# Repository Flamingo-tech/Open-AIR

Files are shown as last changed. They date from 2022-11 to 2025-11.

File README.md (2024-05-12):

# Open AIR

Open AIR is an open-source solution for home ventilation and management through Home Assistant integration. The objective of this project is to develop a versatile ecosystem of Home Assistant-compatible devices that can be easily installed in a wide variety of off-the-shelf ventilation systems, allowing seamless integration into your smart home setup.

The OpenAIR ecosystem is designed to offer the following capabilities:

* Humidity measurement within air ducts
* CO2 level detection in air ducts
* Temperature monitoring inside air ducts
* Default Wi-Fi connectivity
* Full compatibility and control with Home Assistant out of the box
* Adherence to open-source principles

The long-term vision for this project is to create a fully open-source ventilation system that can be 3D printed, preferably using recycled plastics as the primary material.

#### Open AIR Mini:
<p align="center">
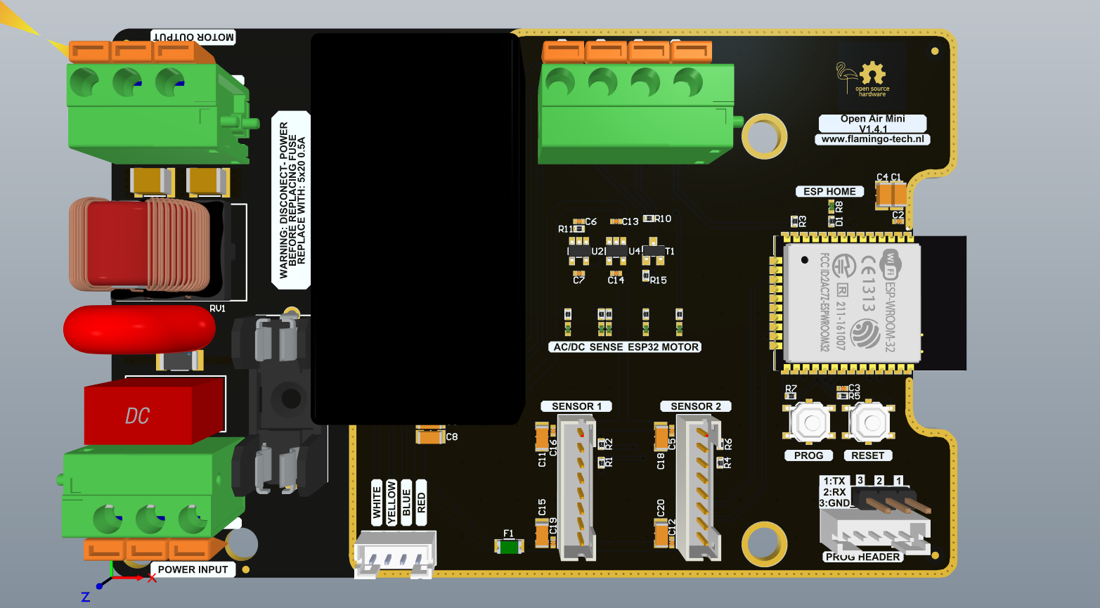
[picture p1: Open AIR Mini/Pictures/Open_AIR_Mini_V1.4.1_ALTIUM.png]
  
</p>

The OpenAIR Mini is a versatile, open-source ventilation controller designed to be compatible with a range of popular ventilation units, including but not limited to:

* DucoBox Silent Standard
* DucoBox Silent Perilex
* DucoBox Silent Connect
* DucoBox Focus (⚠ Note: Original Duco Valves are not supported! ⚠)
* Orcon MVS-15RH
    
Example intergration in HA:
<p align="center">
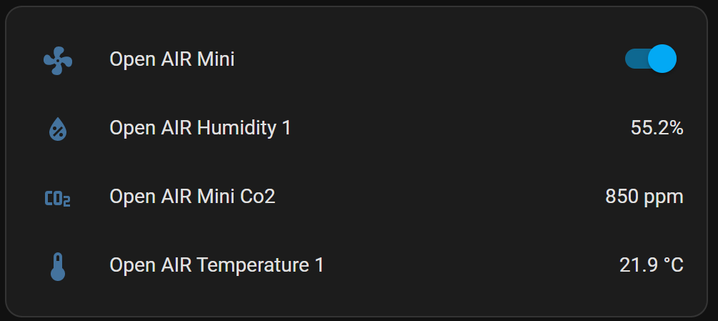
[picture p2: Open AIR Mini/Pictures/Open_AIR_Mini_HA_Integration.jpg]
  
</p>

For more information about the Open AIR Mini see: [Open AIR Mini](https://github.com/Flamingo-tech/Open-AIR/tree/main/Open%20Air%20Mini) 

#### Open AIR Valve:
<p align="center">
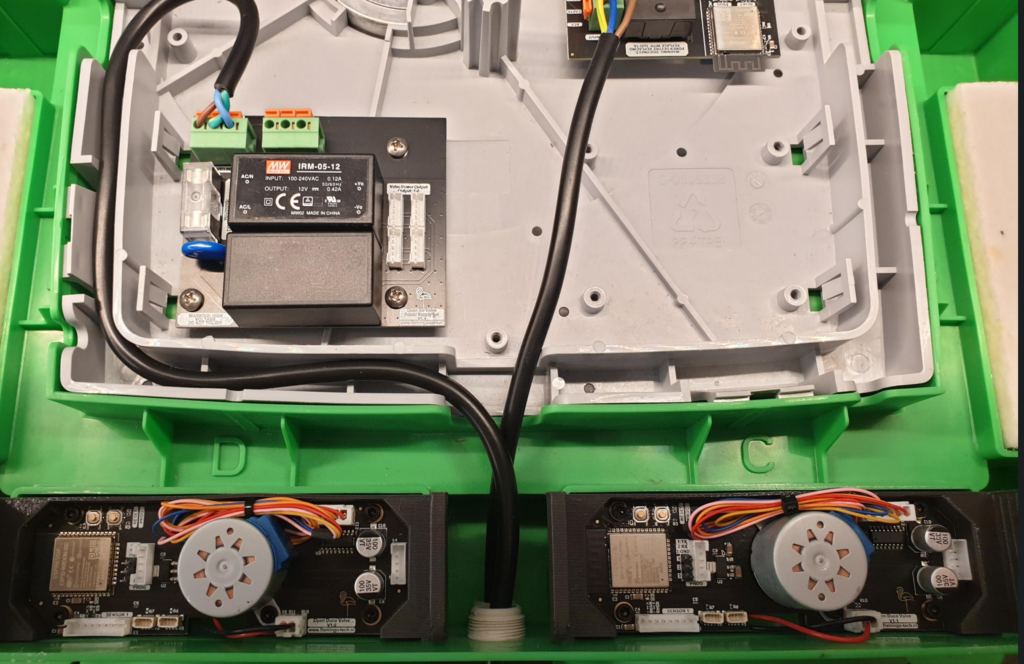
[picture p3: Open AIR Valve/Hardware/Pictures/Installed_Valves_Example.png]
  
</p>

The Open AIR Valve is an open-source valve designed to work with several Duco ventilation boxes, including the DucoBox Silent Standard, DucoBox Silent Perilex, DucoBox Silent Connect, and DucoBox Focus (Note: Original Duco Valves are not supported). It can be fully controlled from Home Assistant, allowing you to set any value between 0-100% open or closed. Additionally, the valve can be connected to one sensor. 

Example intergration in HA:
<p align="center">
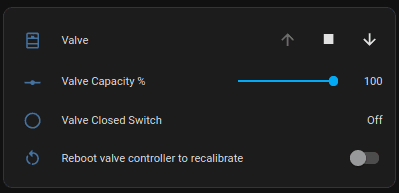
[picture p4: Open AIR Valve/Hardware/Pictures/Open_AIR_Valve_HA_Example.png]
  
</p>

In the future, an external enclosure will be developed for the OpenAIR Valves. This housing can be conveniently installed alongside any ventilation unit, positioned between the unit and the air duct for seamless integration.

For more information about the Open AIR Valve see: [Open AIR Valve](https://github.com/Flamingo-tech/Open-AIR/tree/main/Open%20AIR%20Valve) 

#### Open AIR Sensors
 TODO

# Progress:

| Part: |Done: |Version: |Duco Part Number:|Backwards compatible:|Active:|Store Link:|
|:---|:-----|:---|:---|:---|:---|:---|
|Open AIR Mini |✔️ |V1.3.0 | - |✔️ |✔️ |[Click](https://www.tindie.com/products/theflamingo/open-air-mini-v130/) 
|Open AIR Pro |❌ |- |- |- |❌ |
|Moisture Sensor |✔️ |V2.0.0 | 0000-4218 | ✔️ |✔️ |[Click](https://www.tindie.com/products/theflamingo/open-air-humidity-sensor/)
|CO2 Sensor |✔️ |V2.1.0 | 0000-4216 | ✔️ |❌ |
|Sense Board (RH,Co2,VOC, NOx)|✔️ |V1.0.0 | - | ❌ |✔️ |[Click](https://www.tindie.com/products/theflamingo/open-air-sense-board/)
|Programmer |✔️ |V1.1.0 | - | ✔️ |✔️ |
|Open AIR Valve |✔️ |V1.3.0 |- |❌ |✔️ |[Click](https://www.tindie.com/products/theflamingo/open-air-valve/)
|External Open AIR Valve |❌ |❌ |- |❌ |❌ | 

# Backwards Compatibility

If there is a checkmark in the 'Backwards Compatible' column of the table above, it indicates that you can use the specified device in conjunction with the original Duco Silent ventilation box. For example, you can replace the original Duco moisture/humidity sensor with one of our offerings.

# Special thanks:
[@thomasvnl](https://github.com/thomasvnl) For writing the Valve firmware and valuable feedback.\
[@Septillion](https://github.com/septillion-git) Thanks for providing valuable feedback.\
[@KristofRobberechts ](https://github.com/KristofRobberechts) For providing a beautiful valve design!\
[@slurpgeit](https://github.com/Slurpgeit) Helping write new firmware for the SHT-21 sensor + button software for the Open AIR Mini.

D.Smith For the first version of the installation manual

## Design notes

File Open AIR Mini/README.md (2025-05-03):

# Open AIR Mini

Open AIR Mini is an open-source project that aims to provide firmware and hardware for home ventilation boxes. The project has several goals, including open-source hardware and software, Wi-Fi connectivity, full controllability by Home Assistant, temperature-based ventilation, backward compatibility with Duco sensors, and support for different home ventilation boxes.

## The Hardware
<p align="center">
  
</p>
Open AIR mini installed on DucoBox system:
<p align="center">
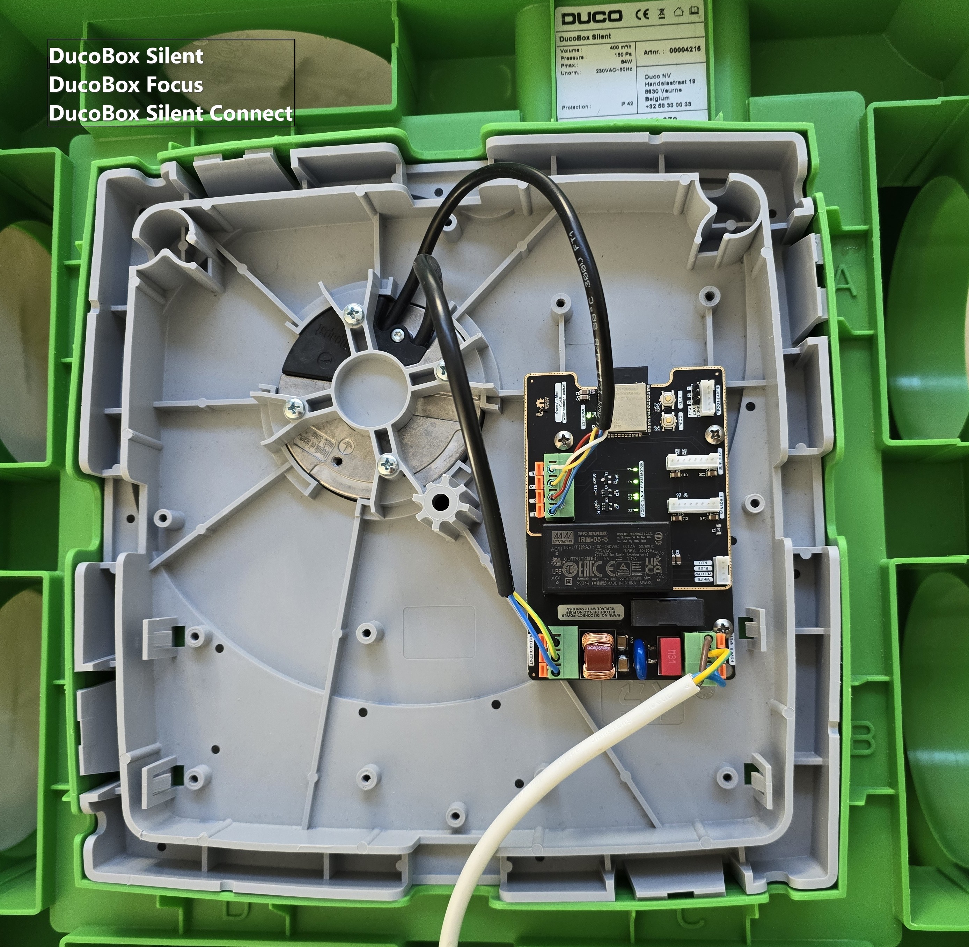
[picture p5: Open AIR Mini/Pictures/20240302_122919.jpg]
  
</p>
The Open AIR Mini hardware supports two sensors on the main board, Wi-Fi connectivity, Home Assistant integration via the ESPHome interface, OTA support, two sensor connectors, a robust power design, and status LEDs. The device is installed by connecting it to the ventilation box, and it can work with different home ventilation boxes. 

Open AIR mini installed on Orcon system:
<p align="center">
  
</p>
Since version V1.4.0 the Open AIR Mini can be directly installed in the ORCON MVS-15XX series of boxes. The original Orcon sensors and RF stuff is not supported! However we are working to make all the Open AIR Sensors compatible :)
On the Orcon systems only a single sensor is supported

### Status LEDS
<p align="center">
  
</p>

The Open AIR Mini from version V1.3.0 and above include five LEDs. The first LED (AC/DC) indicates the status of the Meanwell AC-> DC Converter, and if it is off, the device has no 230VAC power. The second and third LEDs (Sense LED and Sense LED 2) indicate the 5V and 3.3V sensor power, respectively. The fourth LED (ESP32 LED) indicates the 3.3V power supply for the ESP32, and the fifth LED (Motor) indicates the 10V output from the motor. All LEDs should be on in normal operation. 

The ESP32 has a status LED located under it, which displays three different statuses. It blinks slowly (about every second) when a warning is active, blinks quickly (multiple times per second) when an error is active, and stays off otherwise.

## Supported Ventilation Boxes
⚠No RF devices are supported⚠
The Open AIR Mini works with the following ventilation boxes:
 - DucoBox Silent Standard
 - DucoBox Silent Perilex
 - DucoBox Silent Connect
 - DucoBox Reno Non Perilex and Perilex
 - DucoBox Focus (Warning: Original Duco Valves are not supported!)
 - Orcon MVS-15xx
 - and more (see schematic below)
 
 If your home ventilation motor supports the following connections (See image below) Then you can use the Open Air Mini
  
 
The following pins need to be available:

230 Vac directly to the motor
 - 1 Protective earth
 - 2 Power Supply 230VAC 50-60Hz
 - 3 Neutral conductor
 
 Control cabling:
 - 4 GND (on ebmpapst motors BLUE)
 - 5 Tach output (on ebmpapst motors WHITE)
 - 6 10V Output (on ebmpapst motors RED)
 - 7 0-10V PWM Input (on ebmpapst motors YELLOW)

# ⚠ Important

Please note that this project is not supported by Duco and Orcon, and there is no affiliation or technical support from these companies. Modifying your ventilation box is done at your own risk.

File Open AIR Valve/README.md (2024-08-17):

# Open AIR Valve
The Open AIR Valve is an open-source valve designed to work with several Duco ventilation boxes, including the DucoBox Silent Standard, DucoBox Silent Perilex, DucoBox Silent Connect, and DucoBox Focus (Note: Original Duco Valves are not supported). It can be fully controlled from Home Assistant, allowing you to set any value between 0-100% open or closed. Additionally, the valve can be connected to one sensor. 

## The Hardware
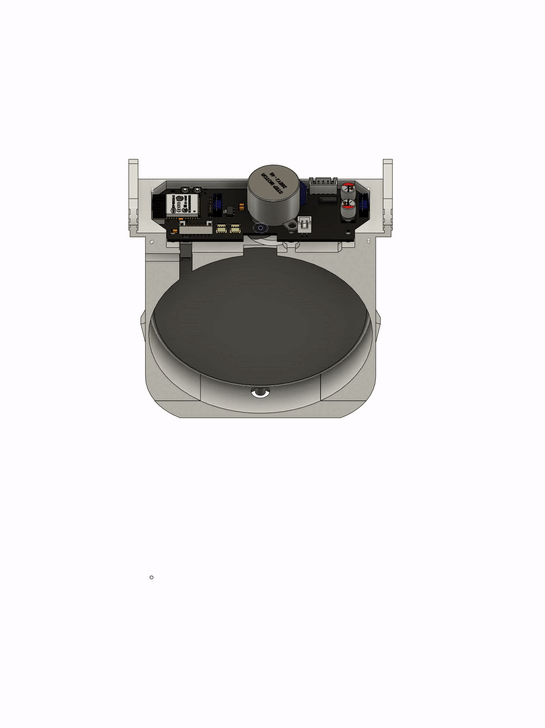
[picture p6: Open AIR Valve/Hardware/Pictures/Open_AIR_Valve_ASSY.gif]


Installed AIR Valve example:


### Status LEDs
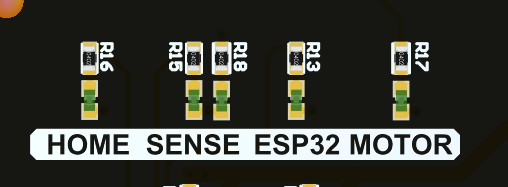
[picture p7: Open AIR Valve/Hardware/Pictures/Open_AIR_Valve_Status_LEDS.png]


The Open AIR Valve from version V1.3.0 and higher contains five LEDs. The first LED (HOME) indicates the status of the Home switch. When it is on, the valve is closed. The second and third LEDs (Sense LED and Sense LED 2) indicate the 5V and 3.3V sensor power, respectively. The fourth LED (ESP32 LED) indicates the 3.3V power supply for the ESP32, and the fifth LED (Motor) indicates the 12V power supply for the motor. All LEDs (except for the HOME LED, which depends on the position of the valve) should be on during normal operation.

# ⚠ Important

Please note that this project is not supported by Duco and Orcon, and there is no affiliation or technical support from these companies. Modifying your ventilation box is done at your own risk.

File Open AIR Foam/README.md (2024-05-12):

# AIR Foam
 Is a simple foam block that can be inserted into the following ducoboxes:
 - DucoBox Silent Standard
 - DucoBox Silent Perilex
 - DucoBox Silent Connect
 - DucoBox Focus
 
 This will silence your Ducobox a bit. I tested with a calibrated Mini DSP microphone and captured the before and after installation.
 
 This is at maximum speed (before foam):
 <p align="center">
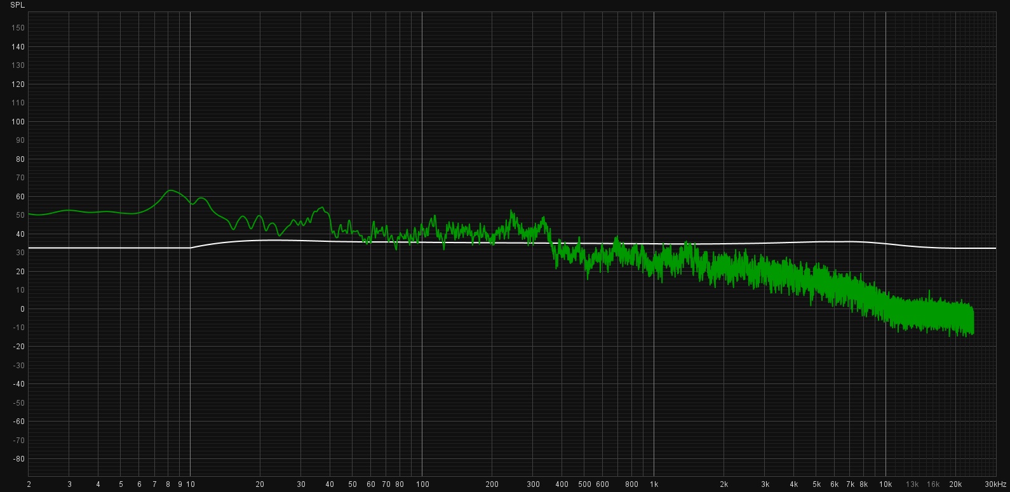
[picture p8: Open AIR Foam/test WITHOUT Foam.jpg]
  
</p>
 And then with foam installed:
 <p align="center">
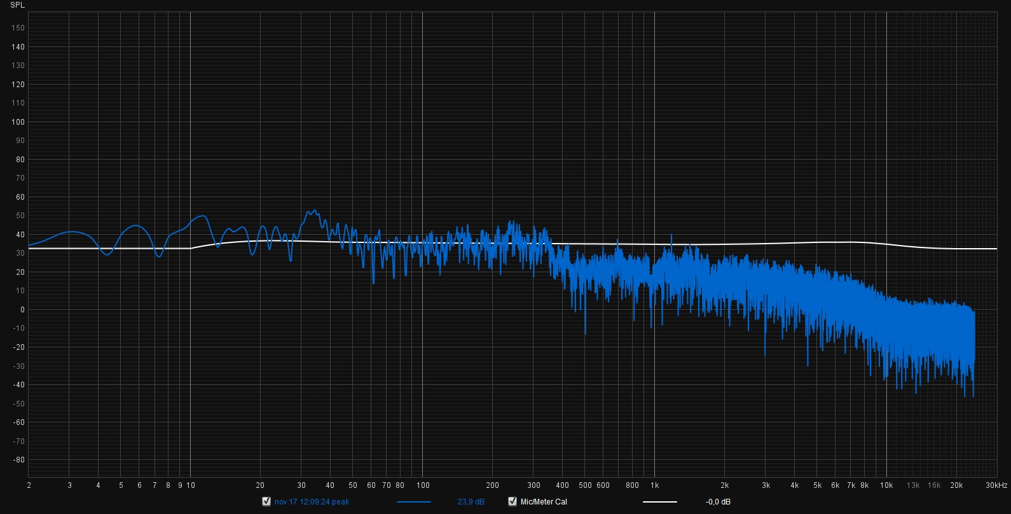
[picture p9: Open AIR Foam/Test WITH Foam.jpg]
  
</p>

 This foam has the following dimensions:
 
 Length: 15CM\
 Width: 12CM\
 Thickness: 4CM\
 Used foam: SG120
 
 You can buy it precut to the above size here : [Schuimwinkel](https://www.schuimwinkel.nl/polypress-sg-120-op-maat.html)

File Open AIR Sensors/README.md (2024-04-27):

PCB's and all files related to them are comming :)

Housing Step files can be found in the above folder! Happy printing!

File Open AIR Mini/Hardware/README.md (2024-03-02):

# Open AIR Mini Source Files
Welcome to the Open AIR Mini source files repository! This is where you can find all the necessary files for each release of Open AIR Mini.

Each release includes the following files:

**Assy Drawing:** text This file contains essential information about the PCBA layer stack, fabrication details, the size of the PCBA, component designators and their locations, as well as a 3D view of the part.

**Schematic Drawing:** This file provides the schematic of the PCBA, giving an overview of the circuit's connections.

**B.O.M File:** This file lists all the parts with their respective MPNs (manufacturer part numbers) and manufacturers, organized by designator.

**Gerber Files:** These files are used to order the bare PCBA's, allowing for accurate production of the circuit boards.

**Step File:** This file contains a 3D model of the PCBA, which can be used for visualization and design purposes.

We hope you find these files helpful in your project development process. Please feel free to contact us if you have any questions or feedback.

**Changelog:**
V1.3.X -> V1.4.0 & V1.4.1
Added support for Orcon MVS-15xx boxes. Now these boxes can be used without any modifications.

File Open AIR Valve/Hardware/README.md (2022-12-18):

# Open AIR Valve
Here you find the following:\
Open AIR Valve PCB Overview_A.pdf: An overview of all the connectors and pinouts used in the Open AIR Valve\
Open AIR Valve Assy B.O.M_A.pdf : An overview of all the different assembly parts needed to assemble a complete Open AIR Valve\
Open AIR Valve PCBA: Gerbers and Schematic op the Open AIR Valve\
Open AIR Valve 3D prints: The location for the 3D print files 

Happy making ^^

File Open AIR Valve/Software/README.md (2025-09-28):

# ESPHome Open Air Valve

Visit https://esphome.io/ for instructions on how to deploy this firmware.

More documentation might come available in future updates. Make sure to copy `example.secrets.yaml` to `secrets.yaml` and fill it with your own wifi credentials.

Change the "X" in `open-air-valve.yaml` with a number or a letter. This will help you identify the Open AIR Valves.

## Hall Sensor Homing

Since hardware version V1.4.0 of the Open AIR Valve , the Omron Switch is changed for a more reliable mechanism: A hall sensor.
The signal of the sensor is inverted! so a small change to your YAML file is needed if you upgrade.

```yaml
binary_sensor:
  - platform: gpio
    id: valve_homing_switch
    pin:
      number: GPIO35
      inverted: true #Change this to "false" if you hava a homing switch from pre V1.4.0 Open AIR Valve.
    name: "Valve Closed Switch"
```

## Sensors

The following sensors are supported right away, either via ESPHome or via a custom implementation.

### New Sensors:
All Valves are now shipped with these sensors:
1. [SHT-20](#sensor-support-SHT-20)
1. [SCD-40](#sensor-support-SCD-4X)
1. [SGP-41](#sensor-support-SGP-41)
1. [SCD-40 & SGP-41 Combination Sensor](#SCD-40-&-SGP-41-Combination-Sensor)

### Old Sensors:
1. [SHT-31](#sensor-support-sht-31)
1. [Senseair S8](#sensor-support-senseair-s8)
1. [SHT-31 & Senseair S8 Combination Sensor](#Using-the-Combination-Sensor-with-Senseair-S8-&-SHT-31-on-the-same-board)

## New:

### Sensor Support: SHT-20

If you have a SHT-20 Sensor add the following code at the bottom of `open-air-valve.yaml` 

```yaml
external_components:
  - source: github://dmaasland/esphome@sht2x
    components: [ sht2x ]
```

```yaml
  - platform: sht2x
    i2c_id: i2c_sensor_1
    temperature:
      name: "${upper_devicename} Temperature"
      id: air_temperature
      accuracy_decimals: 2
    humidity:
      name: "${upper_devicename} Humidity"
      id: air_humidity
      accuracy_decimals: 2
    update_interval: 30s
```
Thanks @dmaasland : https://github.com/dmaasland/esphome/tree/sht2x/esphome/components/sht2x

### Sensor Support: SCD-4X

More info about this sensor and ESPhome : https://esphome.io/components/sensor/scd4x.html

If you want to add a SCD-40 moisture & Temperature sensor & Co2 sensor to the Open AIR Mini, add the following code at the bottom of the `open-air-valve.yaml` file.

```yaml
sensor:
  - platform: scd4x
    i2c_id: i2c_sensor_1 
    co2:
      name: "${upper_devicename} CO2"
      id: air_Co2
      accuracy_decimals: 0
    temperature:
      name: " ${upper_devicename} Temperature"
      id: air_temperature
      accuracy_decimals: 2
    humidity:
      name: " ${upper_devicename} Humidity"
      id: air_humidity
      accuracy_decimals: 2
    update_interval: 30s
    measurement_mode: periodic
```

### Sensor Support: SGP-41

More info about this sensor and ESPhome : https://esphome.io/components/sensor/sgp4x.html & https://esphome.io/components/sensor/scd4x.html

If you want to add a combination sensor SCD-40 moisture & Temperature sensor & Co2 sensor & SGP-41 VOC & NOx to the Open AIR Mini, add the following code at the bottom of the `open-air-valve.yaml` file.

```yaml
sensor:
  - platform: sgp4x
    i2c_id: i2c_sensor_1 
    voc:
      name: "${upper_devicename} VOC Index"
      id: air_VOC
    nox:
      name: "${upper_devicename} NOx Index"
      id: air_NOx
    compensation:
      temperature_source: air_temperature #Make sure to match these if you change ID's.
      humidity_source: air_humidity       #Make sure to match these if you change ID's.
    update_interval: 30s
```

### Sensor Support: SCD-40 & SGP-41 Combination Sensor

More info about this sensor and ESPhome : https://esphome.io/components/sensor/sgp4x.html

If you want to add a SGP-41 VOC & NOx to the Open AIR Mini, add the following code at the bottom of the `open-air-valve.yaml` file.

```yaml
sensor:
  - platform: scd4x
    i2c_id: i2c_sensor_1 
    co2:
      name: "${upper_devicename} CO2"
      id: air_Co2
      accuracy_decimals: 0
    temperature:
      name: "${upper_devicename} Temperature"
      id: air_temperature
      accuracy_decimals: 2
    humidity:
      name: "${upper_devicename} Humidity"
      id: air_humidity
      accuracy_decimals: 2
    update_interval: 30s
    measurement_mode: periodic

  - platform: sgp4x
    i2c_id: i2c_sensor_1 
    voc:
      name: "${upper_devicename} VOC Index"
      id: air_VOC
    nox:
      name: "${upper_devicename} NOx Index"
      id: air_NOx
    compensation:
      temperature_source: air_temperature #Make sure to match these if you change ID's.
      humidity_source: air_humidity       #Make sure to match these if you change ID's.
    update_interval: 30s
```

## Old:

### Sensor Support: SHT-31

More info about this sensor and ESPhome : https://esphome.io/components/sensor/sht3xd.html

If you want to add a SHT-31 moisture & Temperature sensor to the Open AIR Mini, add the following code at the bottom of the `open-air-valve.yaml` file.

```yaml
sensor:
  - platform: sht3xd
    i2c_id: i2c_sensor_1
    temperature:
      name: "${upper_devicename} Temperature"
      id: air_temperature
    humidity:
      name: "${upper_devicename} Humidity"
      id: air_humdity
    address: 0x44
    update_interval: 60s
```

### Sensor Support: Senseair S8

More info about this sensor and ESPhome : https://esphome.io/components/sensor/senseair.html?highlight=co2+senseair

If you want to add a Senseair S8 Co2 sensor to the Open AIR Valve. Add the following code at the bottom of `open-air-valve.yaml` 

```yaml
sensor:
  - platform: senseair
    uart_id: uart_sensor_1
    co2:
      name: "${upper_devicename} CO2"
    update_interval: 60s
```

### Using the Combination Sensor with Senseair S8 & SHT-31 on the same board

If you want to use this specific combination sensor, add the following to the bottom of the `open-air-valve.yaml` file.

```yaml
sensor:
  - platform: sht3xd
    i2c_id: i2c_sensor_1
    temperature:
      name: "${upper_devicename} Temperature"
      id: air_temperature
    humidity:
      name: "${upper_devicename} Humidity"
      id: air_humidity
    address: 0x44
    update_interval: 60s
  - platform: senseair
    uart_id: uart_sensor_1
    co2:
      name: "${upper_devicename} CO2"
      id: air_co2
    update_interval: 60s
```

## Disconnected Mode

When Home Assistant cannot be reached, either because of a lack of WiFi connection or the Home Assistant server being unavailable, a `disconnected mode` has been added to provide basic functionality to the Open AIR Valve unit. This mode will allow the unit to continue standalone. When losing connection to Home Assistant or to your WI-FI network the valve will open automatically.

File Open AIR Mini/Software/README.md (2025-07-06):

# ESPHome Open AIR Mini

Visit https://esphome.io/ for instructions on how to deploy this firmware.

More documentation might come available in future updates. 

## Before you begin

Make sure to copy `example.secrets.yaml` to `secrets.yaml` and fill it with your own WiFi credentials.

## Different communication busses
Depending on what sensor is connected to what connector you need to declare the uart and/or I<sup>2</sup>C busses. If using one sensor, only one (uart/I<sup>2</sup>C) bus is required. In some cases, multiple busses are required for using multiple sensors with the same hardware id (for I<sup>2</sup>C) or if they do not support a hardware id (for uart).

For example, for uart:
```C++
#choose between:
uart_id: uart_sensor_1 // Only used for the Senseair S8 CO2 sensor (Original Duco Co2 Sensor)
uart_id: uart_sensor_2 // Only used for the Senseair S8 CO2 sensor (Original Duco Co2 Sensor)
```

For example, for I<sup>2</sup>C
```C++
i2c_id: i2c_sensor_1 // Used for RH , Co2 , Nox and VOc sensors
i2c_id: i2c_sensor_2 // Used for RH , Co2 , Nox and VOc sensors
```
Example:
```yaml
sensor:
  - platform: sht3xd
    i2c_id: i2c_sensor_1
    temperature:
      name: "Temperature Open AIR Mini x"
      id: air_temperature
    humidity:
      name: "Humidity Open AIR Mini x"
      id: air_humidity
    address: 0x44
    update_interval: 60s

#or
sensor:
  - platform: senseair
    uart_id: uart_sensor_1
    co2:
      name: "CO2 Open AIR Mini x"
    update_interval: 60s
```

## Sensors

The following sensors are supported right away, either via ESPHome or via a custom implementation.

### New Sensors:
All Open AIR Minis are now shipped with these sensors:
1. [SHT-4x](#sensor-support-SHT-4x)
1. [SCD-40](#sensor-support-SCD-4X)
1. [SGP-41](#sensor-support-SGP-41)
1. [SCD-40 & SGP-41 Combination Sensor](#SCD-40-&-SGP-41-Combination-Sensor)

### Old Sensors:
1. [SHT-31](#sensor-support-sht-31)
1. [Senseair S8](#sensor-support-senseair-s8)
1. [SHT-31 & Senseair S8 Combination Sensor](#Using-the-Combination-Sensor-with-Senseair-S8-&-SHT-31-on-the-same-board)
1. [SHT-20](#sensor-support-SHT-20)

## New:

### Sensor Support: SHT-4X

If you have a SHT-4X Sensor add the following code at the bottom of `open-air-mini.yaml` 

```yaml
sensor:
  - platform: sht4x
    i2c_id: i2c_sensor_1
    temperature:
      name: "Open AIR Mini x Temperature"
      id: air_temperature
      accuracy_decimals: 2
    humidity:
      name: "Open AIR Mini x Humidity"
      id: air_humidity
      accuracy_decimals: 2
    update_interval: 30s
```

### Sensor Support: SCD-4X

More info about this sensor and ESPhome : https://esphome.io/components/sensor/scd4x.html

If you want to add a SCD-40 moisture & Temperature sensor & Co2 sensor to the Open AIR Mini, add the following code at the bottom of the `open-air-mini.yaml` file.

```yaml
sensor:
  - platform: scd4x
    i2c_id: i2c_sensor_1 
    co2:
      name: "Open AIR Mini x CO2"
      id: air_Co2
      accuracy_decimals: 0
    temperature:
      name: " Open AIR Mini x Temperature"
      id: air_temperature
      accuracy_decimals: 2
    humidity:
      name: " Open AIR Mini x Humidity"
      id: air_humidity
      accuracy_decimals: 2
    update_interval: 30s
    measurement_mode: periodic
```

### Sensor Support: SGP-41

More info about this sensor and ESPhome : https://esphome.io/components/sensor/sgp4x.html & https://esphome.io/components/sensor/scd4x.html

If you want to add a combination sensor SCD-40 moisture & Temperature sensor & Co2 sensor & SGP-41 VOC & NOx to the Open AIR Mini, add the following code at the bottom of the `open-air-mini.yaml` file.

```yaml
sensor:
  - platform: sgp4x
    i2c_id: i2c_sensor_1 
    voc:
      name: "VOC Index Mini x"
      id: air_VOC
    nox:
      name: "NOx Index Mini x"
      id: air_NOx
    compensation:
      temperature_source: air_temperature #Make sure to match these if you change ID's.
      humidity_source: air_humidity       #Make sure to match these if you change ID's.
    update_interval: 30s
```

### Sensor Support: SCD-40 & SGP-41 Combination Sensor

More info about this sensor and ESPhome : https://esphome.io/components/sensor/sgp4x.html

If you want to add a SGP-41 VOC & NOx to the Open AIR Mini, add the following code at the bottom of the `open-air-mini.yaml` file.

```yaml
sensor:
  - platform: scd4x
    i2c_id: i2c_sensor_1
    co2:
      name: "Open AIR Mini Sensor Mini x CO2"
      id: air_Co2
      accuracy_decimals: 0
    temperature:
      name: "Open AIR Mini Sensor Mini x Temperature"
      id: air_temperature
      accuracy_decimals: 2
    humidity:
      name: "Open AIR Mini Sensor Mini x Humidity"
      id: air_humidity
      accuracy_decimals: 2
    update_interval: 30s
    measurement_mode: periodic

  - platform: sgp4x
    i2c_id: i2c_sensor_1 
    voc:
      name: "Open AIR Mini x VOC Index "
      id: air_VOC
    nox:
      name: "Open AIR Mini x NOx Index "
      id: air_NOx
    compensation:
      temperature_source: air_temperature #Make sure to match these if you change ID's.
      humidity_source: air_humidity       #Make sure to match these if you change ID's.
    update_interval: 30s
```

## Old:

### Sensor Support: SHT-31

More info about this sensor and ESPhome : https://esphome.io/components/sensor/sht3xd.html

If you want to add a SHT-31 moisture & Temperature sensor to the Open AIR Mini, add the following code at the bottom of the `open-air-mini.yaml` file.

```yaml
sensor:
  - platform: sht3xd
    i2c_id: i2c_sensor_1
    temperature:
      name: "Temperature Open AIR Mini x"
      id: air_temperature
    humidity:
      name: "Humidity Open AIR Mini x"
      id: air_humdity
    address: 0x44
    update_interval: 60s
```
### Sensor Support: SHT-20

If you have a SHT-20 Sensor add the following code at the bottom of `open-air-mini.yaml` 

```yaml
external_components:
  - source: github://dmaasland/esphome@sht2x
    components: [ sht2x ]
```

```yaml
  - platform: sht2x
    i2c_id: i2c_sensor_1
    temperature:
      name: "Open AIR Mini x Temperature"
      id: air_temperature
      accuracy_decimals: 2
    humidity:
      name: "Open AIR Mini x Humidity"
      id: air_humidity
      accuracy_decimals: 2
    update_interval: 30s
```
Thanks @dmaasland : https://github.com/dmaasland/esphome/tree/sht2x/esphome/components/sht2x

### Sensor Support: Senseair S8

More info about this sensor and ESPhome : https://esphome.io/components/sensor/senseair.html?highlight=co2+senseair

If you want to add a Senseair S8 Co2 sensor to the Open AIR Valve. Add the following code at the bottom of `open-air-valve.yaml` 

```yaml
sensor:
  - platform: senseair
    uart_id: uart_sensor_1
    co2:
      name: "CO2 Open AIR Mini x"
    update_interval: 60s
```

### Using the Combination Sensor with Senseair S8 & SHT-31 on the same board

If you want to use this specific combination sensor, add the following to the bottom of the `open-air-valve.yaml` file.

```yaml
sensor:
  - platform: sht3xd
    i2c_id: i2c_sensor_1
    temperature:
      name: "Temperature Open AIR Mini x"
      id: air_temperature
    humidity:
      name: "Humidity Open AIR Mini x"
      id: air_humidity
    address: 0x44
    update_interval: 60s
  - platform: senseair
    uart_id: uart_sensor_1
    co2:
      name: "CO2 Open AIR Mini x"
      id: air_co2
    update_interval: 60s
```

###  Notes on using multiple sensors

Change all the 'x' in the document to a number or a letter if you are using multiple sensors and want to be able to clearly identify which is which, and also to prevent conflicts in id namings. If sensors have identical names they wont show up in HA.

## Disconnected Mode

When Home Assistant cannot be reached, either because of a lack of WiFi connection or the Home Assistant server being unavailable, a `disconnected mode` has been added to provide basic functionality to the Open AIR Mini unit. This mode will allow the unit to continue standalone, which in combination with a humidity sensor even allows for different fan speeds activated by humidity levels.

### Disconnected Mode without Humidity Sensor

When the humidity sensor is not connected, the disconnected mode will only allow for the fan to run at a constant speed.

The fan speed can be set in the `open-air-mini.yaml` file by changing the global variable `disconnected_default_fan_speed` to a value between 0 and 100.

To use the Open AIR Mini in disconnected mode without a humidity sensor, in the `open-air-mini.yaml` file, make sure to use the `!include disconnected-mode-without-humidity-sensor.yaml` line in the `script` section. Make sure that the other include is commented out.

### Disconnected Mode With Humidity Sensor

When the humidity sensor is connected, the disconnected mode will allow for the fan to run at a variable speed based on the humidity level.

The different fan speeds and thresholds can be set in the `open-air-mini.yaml` file by changing the global variables that correspond to the different fan speeds and humidity thresholds (see inline comments).

To use the Open AIR Mini in disconnected mode with a humidity sensor, such a sensor has to be configured in the `open-air-mini.yaml`, and in the `script` section, make sure to use the `!include disconnected-mode-with-humidity-sensor.yaml` line. Make sure that the other include is commented out. The humidity sensor has to be connected to the Open AIR Mini, and the `id` of the humidity sensor has to be `air_humidity`.

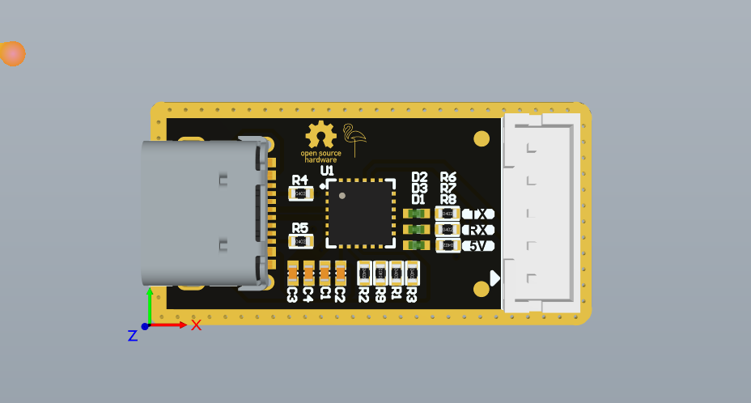
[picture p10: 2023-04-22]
Open AIR Programmer/Hardware/Pictures/Open_AIR_Programmer_V1.1.0.png

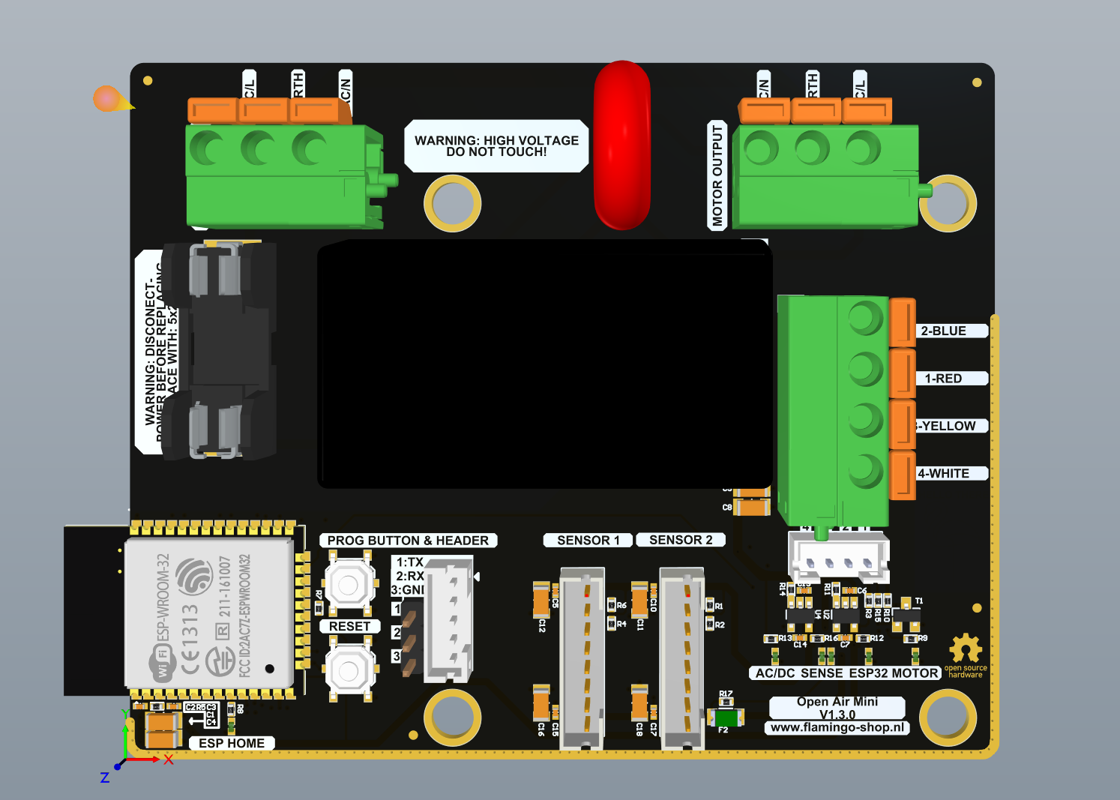
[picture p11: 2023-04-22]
Open Air Mini/Hardware/Pictures/Open_AIR_Mini_V1.3.0.jpg

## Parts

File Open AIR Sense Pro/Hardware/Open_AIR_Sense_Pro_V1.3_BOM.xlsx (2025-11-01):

Name | Description | Designator | Quantity
53261-0571 | Board Connector, 5 Contact(s), 1 Row(s), Male, Right Angle, 0.049 inch Pitch, Surface Mount Terminal, Locking, Natural Insulator, Receptacle | X7 | 1
B5B-ZR-SM4-TF | Header B5B-ZR-SM4-TF, 1.50mm, 5-contacts, top entry, SMT, /1000/reel | X6 | 1
HR911105A | 100mbit connector with integrated magnetics | X5 | 1
USB4105-GF-A-120 | USB Connector, 24 Contact(s), Female, Right Angle, Solder Terminal, Locking, Receptacle | X4 | 1
B8B-PH-SM4-TB(LF)(SN) | Connector Header, PH Series, 8 Position, 2.00mm, 100V, Surface Mount, Solder, Natural. | X3 | 1
687316124422 | FFC/FPC Connector, 16 Contact(s), 1 Row(s), Female, Straight, 0.02 inch Pitch, Surface Mount Terminal, Locking, Ivory Insulator | X2 | 1
SM04B-SRSS-TB(LF)(SN) | Connector Header, Side Entry, SR Series, 4 Position, 1.00mm, 50V, Surface Mount, Tin, Natural | X1 | 1
WS2812B-2020 | RGB Smart LED | U6, U7, U8, U9 | 4
LAN8720AI-CP-TR-ABC | Ethernet Transceiver | U5 | 1
AP2112K-3.3TRG1 | Fixed Positive LDO Regulator, 3.3V, 0.4V Dropout, CMOS, PDSO5 | U2, U3, U4 | 3
AP22653FDZ-7 | USB Load Switch | U1 | 1
PMZ550UNEYL | MOSFET N-Channel Enhancement SMD 30V 590mA 950mV 670mΩ DFN-1006-3 | T1 | 1
SMTSO20100CTJ | Steel Spacer, M2x10 | SP1, SP2 | 2
ERJ-2RKF1212X | RES ,SMT, 12.1kΩ, 1%, 100mW, 100ppm/°C 0402 | R19 | 1
ERJ-U020R00X | RES ,SMT, 0Ω, 1%, 100mW, 100ppm/°C 0402 | R18, R27 | 2
ERJ-2RKF49R9X | RES ,SMT, 49.9Ω, 1%, 100mW, 100ppm/°C 0402 | R14, R15, R16, R17 | 4
ERJ-2RKF1001X | RES ,SMT, 1kΩ, 1%, 100mW, 100ppm/°C 0402 | R5, R8, R20, R21 | 4
ERJ-2RKF1002X | RES ,SMT, 10kΩ, 1%, 100mW, 100ppm/°C 0402 | R3, R4, R6, R7, R11, R12, R13, R22, R23, R24, R25 | 11
ERJ-2RKF5101X | RES ,SMT, 5.1kΩ, 1%, 100mW, 100ppm/°C 0402 | R1, R2, R9, R10, R26, R28 | 6
ESP32-WROOM-32E | WiFi-Modul 802.11/BT 2, 4-2, 5GHz 150Mb/s | MD1 | 1
74279204 | Ferrite Bead, 1 Function(s), 0.5A, 2 Pin(s) | FB1 | 1
ESD9X5.0ST5G | Trans Voltage Suppressor Diode, 107W, 5V V(RWM), Unidirectional, 1 Element, Silicon | D3, D4, D5, D6 | 4
SMAJ5.0A-13-F | Trans Voltage Suppressor Diode, 400W, 5V V(RWM), Unidirectional, 1 Element, Silicon | D2 | 1
DT1240A-04LP-7 | Trans Voltage Suppressor Diode, 52W, 3.3V V(RWM), Unidirectional, 1 Element, Silicon | D1 | 1
CGA2B3X7R1H104K050BB | CAP MLCC 0402 100nF 10% 50V X7R 0402 | C25 | 1
GRM1555C1H9R0CA01D | CAP MLCC 0402 9pF 0.5% 50V C0G 0402 | C20, C21, C22, C23 | 4
CL05A106MQ5NUNC | CAP MLCC 0402 10uF 20% 6.3V X5R 0402 | C5, C6, C7, C8, C12, C13, C16, C17, C27, C28, C29, C30, C31, C32, C33 | 15
GRM155R61H105ME05D | CAP MLCC 0402 1uF 20% 25V X5R 0402 | C2, C9 | 2
CL05A475MP5NRNC | CAP MLCC 0402 4.7uF 20% 10vV X5R 0402 | C1, C3, C4, C10, C11, C14, C15, C18, C19, C24, C26 | 11

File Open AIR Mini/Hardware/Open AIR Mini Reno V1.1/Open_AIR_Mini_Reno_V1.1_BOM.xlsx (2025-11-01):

Name | Description | Designator | Quantity
CL05A106MQ5NUNC | CAP MLCC 0402 10uF 20% 6.3V X5R 0402 | C1, C2, C3, C9, C17, C18, C21, C22, C28, C29, C30, C31, C32, C33, C34, C36, C37 | 17
GRM155R61H105ME05D | CAP MLCC 0402 1uF 20% 25V X5R 0402 | C4 | 1
CL31A106KBHNNNE | CAP MLCC 1206 10uF 10% 50V X5R | C5, C7, C8 | 3
865230557006 | WCAP-AS5H Aluminum Electrolytic Capacitors | C6, C14 | 2
CGA2B3X7R1H104K050BB | CAP MLCC 0402 100nF 10% 50V X7R 0402 | C10 | 1
GRM1555C1H560JA01J | CAP MLCC 0402 56pF 5% 50V C0G 0402 | C11 | 1
GRM32EC81C476KE15K | CAP MLCC 1210 47uF 10% 16V X7R | C12, C13 | 2
CL05A475MP5NRNC | CAP MLCC 0402 4.7uF 20% 10vV X5R 0402 | C15, C16, C19, C20, C27, C35, C38 | 7
GRM1555C1H1R2BA01D | CAP MLCC 0402 1.2pF 0.1% 50V C0G 0402 | C23, C24, C25, C26 | 0
GRM155R71C103KA01D | CAP MLCC 0402 10nF 10% 16V X7R 0402 | C39, C40 | 2
150060WS75000 | SMD Mono-color Chip LEDs | D1, D4, D5, D8, D9, D11, D12 | 7
SMF24A | Trans Voltage Suppressor Diode, 200W, 24V V(RWM), Unidirectional, 1 Element, Silicon | D6 | 1
DT1240A-04LP-7 | Trans Voltage Suppressor Diode, 52W, 3.3V V(RWM), Unidirectional, 1 Element, Silicon | D7 | 1
BZT52C12-7-F | Zener Diode, 12V V(Z), 5.39%, 0.37W, Silicon, Unidirectional | D10 | 1
1206L050/24WR | PTC Resettable Fuse, Surface Mount | F1 | 1
74279204 | Ferrite Bead, 1 Function(s), 0.5A, 2 Pin(s) | FB1, FB2 | 2
74437336100 | General Purpose Inductor, 10uH, 20%, 1 Element, Powdered Iron-Core, SMD, 2220 | L1 | 1
ESP32-WROOM-32E | WiFi-Modul 802.11/BT 2, 4-2, 5GHz 150Mb/s | MD1 | 1
ERJ-2RKF1001X | RES ,SMT, 1kΩ, 1%, 100mW, 100ppm/°C 0402 | R1, R15, R16, R25, R30, R35, R37 | 7
ERJ-2RKF1801X | RES ,SMT, 1.8kΩ, 1%, 100mW, 100ppm/°C 0402 | R2, R3, R8, R9 | 4
ERJ-2RKF1002X | RES ,SMT, 10kΩ, 1%, 100mW, 100ppm/°C 0402 | R4, R5, R7, R10, R11, R17, R22, R23, R31, R32, R33, R34, R38, R40, R41 | 15
ERJ-2RKF3302X | RES ,SMT, 33kΩ, 1%, 100mW, 100ppm/°C 0402 | R6, R24 | 2
ERJ-2RKF1003X | RES ,SMT, 100kΩ, 1%, 100mW, 100ppm/°C 0402 | R12 | 1
ERJ-2RKF5101X | RES ,SMT, 5.1kΩ, 1%, 100mW, 100ppm/°C 0402 | R13 | 1
ERJ-2RKF1372X | RES ,SMT, 13.7kΩ, 1%, 100mW, 100ppm/°C 0402 | R14 | 1
ERJ-2RKF49R9X | RES ,SMT, 49.9Ω, 1%, 100mW, 100ppm/°C 0402 | R18, R19, R20, R21 | 4
ERJ-2RKF1212X | RES ,SMT, 12.1kΩ, 1%, 100mW, 100ppm/°C 0402 | R26 | 1
ERJ-U020R00X | RES ,SMT, 0Ω, 1%, 100mW, 100ppm/°C 0402 | R27, R28, R29, R36 | 4
0402WGF2200TCE | RES ,SMT, 220Ω, 1%, 63.5mW, 100ppm/°C 0402 | R39 | 1
PTS526SM15SMTR2LFS | Switch Tactile N.O. SPST Round Button Gull Wing 0.05A 12VDC 500000Cycles 1.57N SMD T/R | S1, S2 | 2
2N7002 | Small Signal Field-Effect Transistor, 0.115A I(D), 60V, 1-Element, N-Channel, Silicon, Metal-oxide Semiconductor FET | T1 | 1
SHT40-AD1B-R2 | Senserion Moisture and Temperature Sensor | U1 | 1
TPS54202DDCR | Switching Regulator, Current-mode, 2A, 500kHz Switching Freq-Max, PDSO6 | U2 | 1
AP2112K-3.3TRG1 | Fixed Positive LDO Regulator, 3.3V, 0.4V Dropout, CMOS, PDSO5 | U3, U4, U6 | 3
LAN8720AI-CP-TR-ABC | Ethernet Transceiver | U5 | 1
B5B-PH-SM4-TB(LF)(SN) | B5B-PH-SM4-TB(LF)(SN) | X1 | 1
M20-8770342 | Header SMT MALE 3 Pin 1 Row 2.54mm Pitch Vertical Gold Plated | X2 | 1
B8B-PH-SM4-TB(LF)(SN) | Connector Header, PH Series, 8 Position, 2.00mm, 100V, Surface Mount, Solder, Natural. | X3 | 1
B02P-NV(LF)(SN) | NV Series 2 Position 5 mm Pitch Through Hole Locking Header | X4 | 1
B4P-VH-B(LF)(SN) | Locking Header, Top Entry Type of PBT, 4 Circuit, 3.96mmPitch | X5 | 1
HR911105A | 100mbit connector with integrated magnetics | X6 | 1
B4B-PH-SM4-TB | 2.0mm pitch/Disconnectable Insulation displacement and Crimp style connectors | X7 | 1

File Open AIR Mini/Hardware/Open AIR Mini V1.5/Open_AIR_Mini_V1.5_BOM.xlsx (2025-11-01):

Name | Description | Designator | Quantity
CL31B226MPHNNNE | CAP CER SMT 22uF 20% 10V X7R 1206 | C1, C2, C5, C6, C7, C8 | 6
8853522130151 | Suppression Cap, 2200Pf, Class X1/Y2 | C3, C10 | 2
CL05A475MP5NRNC | CAP MLCC 0402 4.7uF 20% 10vV X5R 0402 | C4, C12, C13, C14, C15 | 5
890324023025CS | Film Capacitor | C9 | 1
150060WS75000 | SMD Mono-color Chip LEDs | D1, D2, D3, D4, D5, D6 | 6
1206L050/24WR | PTC Resettable Fuse, Surface Mount | F1 | 1
696103201002 | Fuses/Accessories | F2 | 1
744822110 | Data Line Filter, 2 Function(s), 250V, 1A, 4 Pin(s) | L1 | 1
BLM15HG102SN1D | Ferrite Chip, 1 Function(s), 0.25A, 2 Pin(s) | L2, L3, L4, L5, L6, L7, L8, L9 | 8
74279204 | Ferrite Bead, 1 Function(s), 0.5A, 2 Pin(s) | L10 | 1
PCB | PCB | PCB1 | 1
ERJ-2RKF1001X | RES ,SMT, 1kΩ, 1%, 100mW, 100ppm/°C 0402 | R1, R5, R20, R21 | 4
ERJ-2RKF1002X | RES ,SMT, 10kΩ, 1%, 100mW, 100ppm/°C 0402 | R2, R3, R4, R9, R10, R11, R17, R19 | 8
ERJ-U020R00X | RES ,SMT, 0Ω, 1%, 100mW, 100ppm/°C 0402 | R6, R7, R8 | 3
0402WGF2200TCE | RES ,SMT, 220Ω, 1%, 63.5mW, 100ppm/°C 0402 | R12 | 1
ERJ-2RKF2201X | RES ,SMT, 2.2kΩ, 1%, 100mW, 100ppm/°C 0402 | R13, R14, R15, R16, R22 | 5
CRCW20101M00FKEF | RES ,SMT, 1MΩ, 1%, 0.75W, 100ppm/°C 2010 | R18 | 1
B72214S301K101 | Varistor, Circuit Protection; 300Vrms; 775V; 4500A; Metal Oxide; 300pF; Wire; 0.6W; 25ns | RV1 | 1
PTS526SM15SMTR2LFS | Switch Tactile N.O. SPST Round Button Gull Wing 0.05A 12VDC 500000Cycles 1.57N SMD T/R | S1, S2 | 2
2N7002 | Small Signal Field-Effect Transistor, 0.115A I(D), 60V, 1-Element, N-Channel, Silicon, Metal-oxide Semiconductor FET | T1 | 1
IRM-05-5 | AC/DC 5W 5V Single Output Power Supply, Encapsulated Board Mount Module | U1 | 1
AP2112K-3.3TRG1 | Fixed Positive LDO Regulator, 3.3V, 0.4V Dropout, CMOS, PDSO5 | U2, U4 | 2
ESP32-WROOM-32E | WiFi-Modul 802.11/BT 2, 4-2, 5GHz 150Mb/s | U3 | 1
B5B-PH-SM4-TB(LF)(SN) | B5B-PH-SM4-TB(LF)(SN) | X1 | 1
M20-8770342 | Header SMT MALE 3 Pin 1 Row 2.54mm Pitch Vertical Gold Plated | X2 | 1
B4B-PH-SM4-TB | 2.0mm pitch/Disconnectable Insulation displacement and Crimp style connectors | X3 | 1
B8B-PH-SM4-TB(LF)(SN) | Connector Header, PH Series, 8 Position, 2.00mm, 100V, Surface Mount, Solder, Natural. | X4, X5 | 2
1790539 | Connector; PCB header; 15A; 320V; 4-position; FFKDSA/V1-5 08- 4 | X6 | 1
1790937 | Connector; PCB header; 15A; 320V; 3-position; FFKDSA/V1-5 08- 3 | X7, X8 | 2

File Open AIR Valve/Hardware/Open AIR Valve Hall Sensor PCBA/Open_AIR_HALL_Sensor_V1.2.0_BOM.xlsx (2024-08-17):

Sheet: Part List Report
 |  |  |  |  |  |  |  |  |  | V1.2.0
 | Bill of Material |  | Open AIR Valve Hall Sensor |  |  |  |  |  |  | <Parameter UpdateNumber not found>
 |  | Source Data From: | OPEN_AIR_VALVE_HALL_SENSOR.BomDoc
 |  | Project: | OPEN_AIR_VALVE_HALL_SENSOR.PrjPcb
 |  | Revision: | V1.2.0.<Parameter UpdateNumber not found>
 |  | Variant: | None
 | Report Date: |  | 17/08/2024 | 12:30
 | Print Date: |  | 2024-08-17 | 13:36:37
# | Print Date: | Quantity | Manufacturer | Manufacturer Part Number | Description | Value | Tolerance | #Column Name Error:' Fitted | Preferred Supplier
1 |  | 1 | Kemet | C0402C104K3RACTU | CAP MLCC 0402 100nF 10% 25V X7R 0402 | 100nF | 10%
2 |  | 1 | Murata | GCM155R71H104KE02J | CAP CER SMT 100nF 10% 50VDC X7R 0402 | 100nF | 10%
3 |  | 1 | Samsung | CL31B106KAHNFNE | CAP MLCC 1206 10uF 10uF 25V X7R 1206 | 10µF | 10%
4 |  | 2 | ONSemiconductor | ESD9X5.0ST5G | Trans Voltage Suppressor Diode, 107W, 5V V(RWM), Unidirectional, 1 Element, Silicon
5 |  | 2 | Panasonic | ERJ-S060R00V | RES ,SMT, 0Ω, 1%, 125mW, 100ppm/°C 0805 | 0 | 1%
6 |  | 1 | Texas Instruments | DRV5032FBDBZR | Hall Effect Sensor, 0.5mT Min, 4.8mT Max, -5.0-5.0mA, Plastic/epoxy, Rectangular, Surface Mount
7 |  | 1 | JST | B3B-XH-A(LF)(SN) | Connector Header, XH Series, 3 Position, 2.50mm, Through Hole, Press-Fit, Solder, Natural
Total: |  | 9 |  | Notes
 |  |  |  | <Parameter BOMNotes not found>

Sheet: Project Information
Project Full Path | C:\Users\Public\Documents\Altium\OPEN_AIR_VALVE_HALL_SENSOR\OPEN_AIR_VALVE_HALL_SENSOR.PrjPcb
Project Filename | OPEN_AIR_VALVE_HALL_SENSOR.PrjPcb
Variant Name | None
Data-Source Filename | OPEN_AIR_VALVE_HALL_SENSOR.BomDoc
Data-Source Full Path | OPEN_AIR_VALVE_HALL_SENSOR.BomDoc
Title | Bill of Materials for BOM Document [OPEN_AIR_VALVE_HALL_SENSOR.BomDoc]
Total Quantity | 9
Report Time | 12:30
Report Date | 17/08/2024
Report Date & Tine | 17/08/2024 12:30
Output Name | Bill of Materials
Output Type | BomReport
Output Generator Name | BOM
Output Generator Description | Bill of Materials

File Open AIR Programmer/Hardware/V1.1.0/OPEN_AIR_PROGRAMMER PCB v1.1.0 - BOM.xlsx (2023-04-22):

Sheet: Part List Report
 | Bill of material |  | Open AIR Programmer
 | Source Data From: |  | OPEN_AIR_PROGRAMMER PCB
 | Project: |  | OPEN_AIR_PROGRAMMER PCB
 | Revision: |  | 1.1.0
 | Variant: |  | None
 | Report Date: |  | 22-4-2023 | 15:31
 | Print Date: |  | 2023-04-22 | 15:35:12
# | Designator | Quantity | Manufacturer | Manufacturer Part Number | Description | Value | Tolerance | #Column Name Error:' Fitted | Preferred Supplier
1 | C1, C3 | 2 | KEMET | C0402C104K3RACTU | CAP CER SMT 100nF 10% 25V X7R 0402 | 100nF | 10%
2 | C2, C4 | 2 | Murata | GRM155R60J475ME47D | CAP CER SMT 4.7uF 20% 6.3V X5R 0402 | 4.7µF | 20%
3 | D1, D2, D3 | 3 | Wurth Electronics | 150040GS73240 | LED SMT Green Chip Waterclear 3.2V 20mA 0402
4 | J1 | 1 | GCT | USB4105-GF-A | USB 2.0 Type C Female Horizontal SMD, PD and USB2.0 only
5 | PCB1 | 1 | Open AIR Programmer | 1.1 | PCB
6 | R1, R2, R3, R8, R9 | 5 | Vishay | CRCW040210K0FKED | RES SMT 10kΩ 1% 62.5mW 100ppm/°C 0402 | 10kΩ | 1%
7 | R4, R5 | 2 | Bourns | CR0402-FX-5101GLF | RES SMT 5.1kΩ 1% 100mW 100ppm/°C 0402 | 5.1kΩ | 1%
8 | R6, R7 | 2 | Panasonic | ERJ-2RKF1001X | RES SMT 1kΩ 1% 100mW 100ppm/°C 0402 | 1kΩ | 1%
9 | U1 | 1 | Silicon Labs | CP2102N-A02-GQFN24 | USB2.0 to UART bridge SMT, 1 port, QFN-24
10 | X1 | 1 | JST | B5B-PH-K-S(LF)(SN) | JST (JAPAN SOLDERLESS TERMINALS) - B5B-PH-K-S(LF)(SN) - Pin Header, Wire-to-Board, 2 mm, 1 Rows, 5 Contacts, Through Hole, PH Series
Total: |  | 20 |  | Notes
 |  |  |  | No notes

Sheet: Project Information
Project Full Path | C:\Users\Public\Documents\Altium\Projects\Private_USB-UART\OPEN_AIR_USB-UART.PrjPcb
Project Filename | OPEN_AIR_USB-UART.PrjPcb
Variant Name | None
Data-Source Filename | OPEN_AIR_USB-UART.PrjPcb
Data-Source Full Path | C:\Users\Public\Documents\Altium\Projects\Private_USB-UART\OPEN_AIR_USB-UART.PrjPcb
Title | Bill of Materials for Project [OPEN_AIR_USB-UART.PrjPcb] (No PCB Document Selected)
Total Quantity | 20
Report Time | 15:31
Report Date | 22-4-2023
Report Date & Tine | 22-4-2023 15:31
Output Name | Bill of Materials
Output Type | BomReport
Output Generator Name | BOM
Output Generator Description | Bill of Materials

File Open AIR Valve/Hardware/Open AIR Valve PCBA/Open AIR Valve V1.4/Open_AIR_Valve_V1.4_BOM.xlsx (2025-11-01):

Name | Description | Designator | Quantity
CL31B226MPHNNNE | CAP CER 22uF 20% 10V X7R 1206 | C1, C5, C7, C10, C11, C13, C14, C15, C16, C17, C18 | 11
C0402C104K3RACTU | CAP CER 100nF 10% 25V X7R 0402 | C2, C4, C6, C12 | 4
GRM155C71A105KE11D | CAP CER 1uF 10% 10V X7S 0402 | C3, C8, C19 | 3
GRM155R60J475ME47D | CAP CER SMT 4.7uF 20% 6.3V X5R 0402 | C9, C20 | 2
150040GS73240 | LED SMT Green Chip Waterclear 3.2V 20mA 0402 | D1, D2, D3, D4, D5, D6 | 6
1206L050/24WR | Resettable fuse 0.5A/24V | F1 | 1
Fiducial |  | FID1, FID2, FID3, FID4 | 4
ERJ-2RKF1001X | RES SMT 1kΩ 1% 100mW 100ppm/°C 0402 | R1, R11, R13, R15 | 4
CRCW040210K0FKED | RES SMD 10kΩ 1% 62.5mW 100PPM 0402 | R2, R3, R10, R12, R14, R16, R17, R18 | 8
ERJ-2RKF2201X | RES SMD 2.2kΩ 1% 100mW 100PPM 0402 | R4, R5 | 2
CRCW04020000Z0EDC | RES SMD 0Ω 1% 62.5mW 100ppm/°C 0402 | R6, R7, R8, R9 | 4
PTS526 SMG15 SMTR2 LFS | Tactile Switch 50mA 12VDC, 5.2x5.2mm, 1.5mm H | S1, S2 | 2
ESP32-WROOM-32E | WiFi (802.11) & Bluetooth (v4.2) Module, SMD, 3.3V, Embedded Antenna | U1 | 1
AP2112K-3.3TRG1 | IC REG LDO 3.3V 0.6A SOT25 | U2, U4 | 2
ULQ2003D1013TR | Darlington Transistors Seven Darlington array | U3 | 1
B5B-PH-K-S(LF)(SN) | JST (JAPAN SOLDERLESS TERMINALS) - B5B-PH-K-S(LF)(SN) - Pin Header, Wire-to-Board, 2 mm, 1 Rows, 5 Contacts, Through Hole, PH Series | X1, X4 | 2
61300311121 | Board-To-Board Connector, Vertical, Wr-Phd Series, Through Hole, Header, 3, 2.54 mm | X2 | 1
B8B-PH-K-S(LF)(SN) | JST (JAPAN SOLDERLESS TERMINALS) - B8B-PH-K-S(LF)(SN) - Pin Header, Wire-to-Board, 2 mm, 1 Rows, 8 Contacts, Through Hole, PH Series | X3 | 1
B3B-XH-A(LF)(SN) | CONN HEADER VERT 3POS 2.5MM | X5 | 1
BM04B-SRSS-TB(LF)(SN) | Header SMT Male 4 Pin 1 Row 1.0mm Pitch Vertical Tin Plated | X6, X8 | 2
B5B-XH-AM(LF)(SN) | Header THT Male 5 Pin 1 Row 2.50mm Pitch Vertical tin Plated | X7 | 1

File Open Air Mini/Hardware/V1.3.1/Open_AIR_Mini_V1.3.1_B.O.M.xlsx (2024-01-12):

 |  |  |  |  |  |  |  |  |  | 1.3.1
 | Bill of material |  | Open AIR Mini |  |  |  |  |  |  | <Parameter UpdateNumber not found>
 | Source Data From: |  | Open_AIR_Mini_V1.3.1_PCB
 | Project: |  | Open_AIR_Mini_V1.3.1_PCB
 | Revision: |  | 1.3.1
 | Variant: |  | None
 | Report Date: |  | 10-4-2023 | 15:27
 | Print Date: |  | 2024-01-04 | 16:09:49
# | Designator | Quantity | Manufacturer | Manufacturer Part Number | Description | Value | Tolerance | #Column Name Error:' Fitted | Preferred Supplier
1 | C1, C4, C5, C8, C9, C11, C16, C18 | 8 | Samsung | CL31B226MPHNNNE | CAP CER 22uF 20% 10V X7R 1206 | 22uF | 20%
2 | C2, C10, C12, C15, C17 | 5 | KEMET | C0402C104K3RACTU | CAP CER 100nF 10% 25V X7R 0402 | 100nF | 10%
3 | C3, C6, C13 | 3 | Murata | GRM155C71A105KE11D | CAP CER 1uF 10% 10V X7S 0402 | 1uF | 10%
4 | C7, C14 | 2 | Murata | GRM155R60J475ME47D | CAP CER SMT 4.7uF 20% 6.3V X5R 0402 | 4.7µF | 20%
5 | D1, D2, D3, D4, D5, D6 | 6 | Wurth Electronics | 150040GS73240 | LED SMT Green Chip Waterclear 3.2V 20mA 0402
6 | F1 | 1 | Wurth Electronics | 696103101002 | FUSEHOLDER BLOCKS - PCB - CLIP C |  |  |  | Wurth Electronics
7 | F2 | 1 | Littelfuse | 1206L050/24WR | Resettable fuse 0.5A/24V
8 | PCB1 | 1 | Open AIR Mini | 1.3.1 | PCB
9 | R1, R2, R4, R6, R17 | 5 | Panasonic | ERJ-2RKF2201X | RES SMD 2.2kΩ 1% 100mW 100PPM 0402 | 2.2kΩ | 1%
10 | R3, R5, R7, R9, R10, R11, R13, R14, R15 | 9 | Vishay | CRCW040210K0FKED | RES SMD 10kΩ 1% 62.5mW 100PPM 0402 | 10kΩ | 1%
11 | R8, R12, R16 | 3 | Panasonic | ERJ-2RKF1001X | RES SMT 1kΩ 1% 100mW 100ppm/°C 0402 | 1kΩ | 1%
12 | RV1 | 1 |  |  | Varistor, Circuit Protection; 300Vrms; 775V; 4500A; Metal Oxide; 300pF; Wire; 0.6W; 25ns
13 | S1, S2 | 2 | C&K | PTS526 SMG15 SMTR2 LFS | Tactile Switch 50mA 12VDC, 5.2x5.2mm, 1.5mm H
14 | T1 | 1 | Nexperia | PMV16XNR | MOSFET, N-Channel, 6.8A, 20V, 16mΩ
15 | U1 | 1 | Espressif | ESP32-WROOM-32E (M113EH3200PS3Q0) | WiFi (802.11) & Bluetooth (v4.2) Module, SMD, 3.3V, Embedded Antenna
16 | U2, U4 | 2 | Diodes | AP2112K-3.3TRG1 | IC REG LDO 3.3V 0.6A SOT25
17 | U3 | 1 |  | IRM-05-5 | AC/DC 5W 5V Single Output Power Supply, Encapsulated Board Mount Module
18 | X1, X5 | 2 | Phoenix Contact | 1790937 | Connector; PCB header; 15A; 320V; 3-position; FFKDSA/V1-5 08- 3
19 | X2 | 1 | Phoenix Contact | 1790539 | Connector; PCB header; 15A; 320V; 4-position; FFKDSA/V1-5 08- 4
20 | X3 | 1 | JST | B5B-PH-K-S(LF)(SN) | JST (JAPAN SOLDERLESS TERMINALS) - B5B-PH-K-S(LF)(SN) - Pin Header, Wire-to-Board, 2 mm, 1 Rows, 5 Contacts, Through Hole, PH Series
21 | X4, X6 | 2 | JST | B8B-PH-K-S(LF)(SN) | JST (JAPAN SOLDERLESS TERMINALS) - B8B-PH-K-S(LF)(SN) - Pin Header, Wire-to-Board, 2 mm, 1 Rows, 8 Contacts, Through Hole, PH Series
22 | X7 | 1 | Wurth Elektronik | 61300311121 | Board-To-Board Connector, Vertical, Wr-Phd Series, Through Hole, Header, 3, 2.54 mm
23 | X8 | 1 | JST | B4B-PH-K-S(LF)(SN) | Header THT Male 4 Pin 1 Row 2mm Pitch Vertical Tin Plated
Total: |  | 60 |  | Notes
 |  |  |  | <Parameter BOMNotes not found>

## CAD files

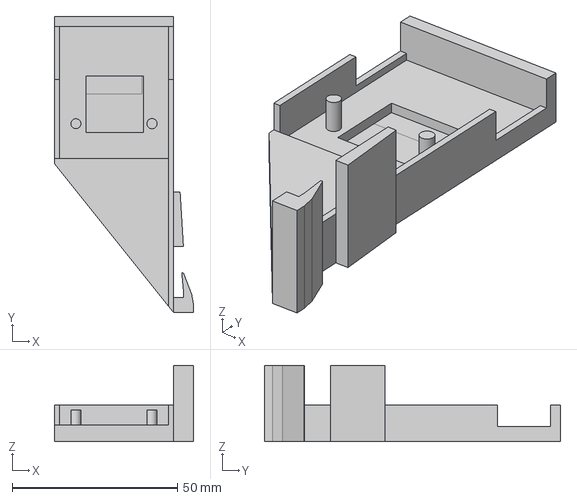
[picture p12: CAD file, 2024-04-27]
Open AIR Sensors/Open AIR Sensor Housing/Duco Sensor Housing/Open_AIR_Sensor_Housing_Duco_Bottom_B.step
42.1 x 89.5 x 23.0 mm

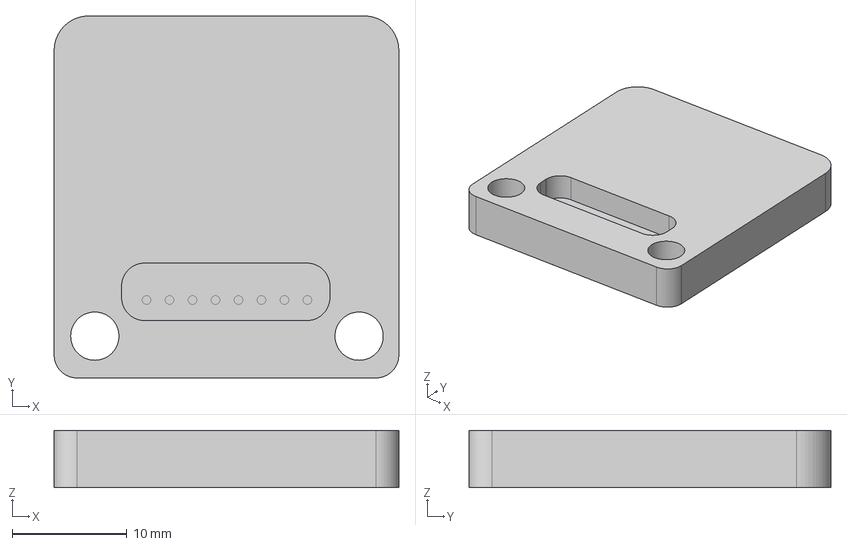
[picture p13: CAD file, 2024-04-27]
Open AIR Sensors/Open AIR Sensor Housing/Orcon Sensor Housing/Open_AIR_Sensor_Housing_Orcon_B.step
30.0 x 31.5 x 5.00 mm

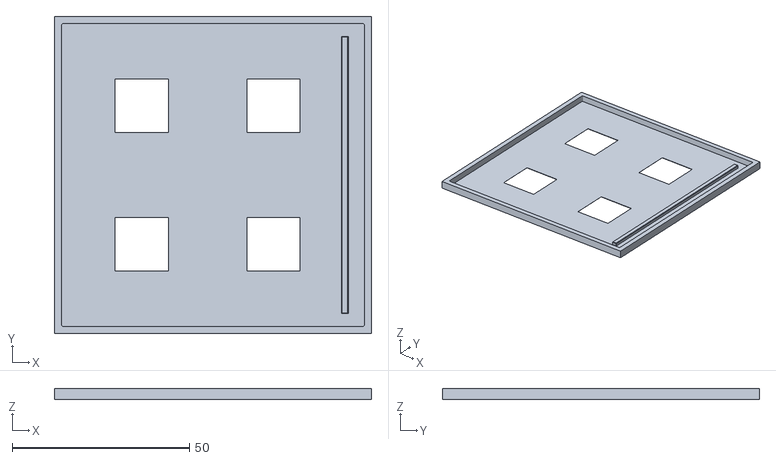
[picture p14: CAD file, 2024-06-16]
Open AIR Stickers/Sticker Align Jig/ESW-0ZAA-EU-Sticker Align Jig.obj
89.4 x 89.4 x 3.00

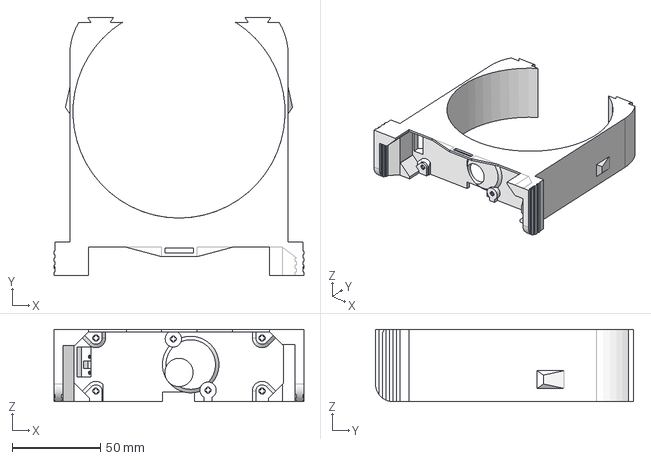
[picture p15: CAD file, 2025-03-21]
Open AIR Valve/Hardware/Open AIR Valve 3D prints/NEW (Hall Sensor)/Open_AIR_Valve_Top_C.step
141.4 x 146.0 x 40.9 mm

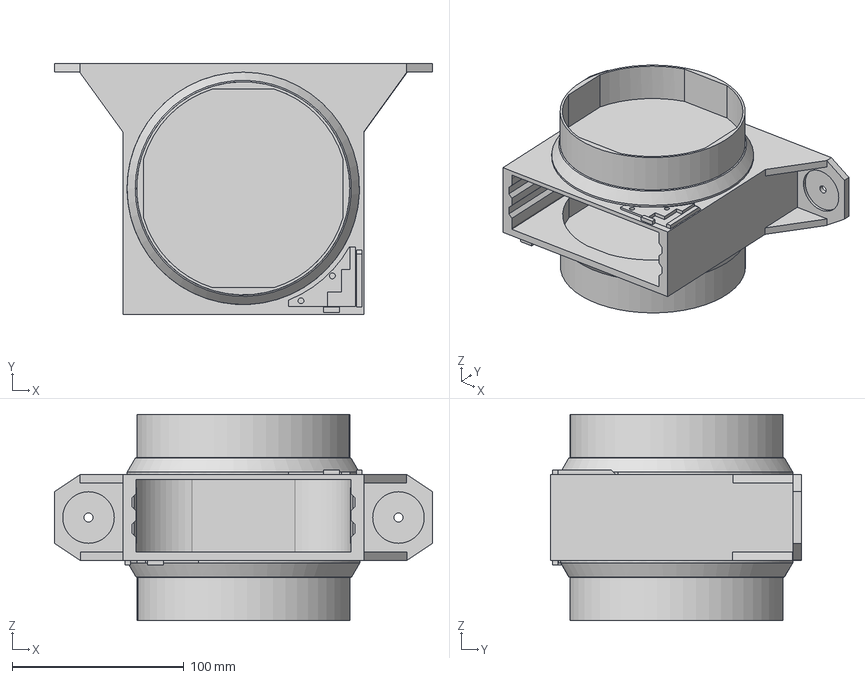
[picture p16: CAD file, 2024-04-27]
Open AIR Valve_External/Hardware/Open AIR Valve 3D prints/Open_AIR_Valve_External_Housing_A.step
220.0 x 146.0 x 120.0 mm

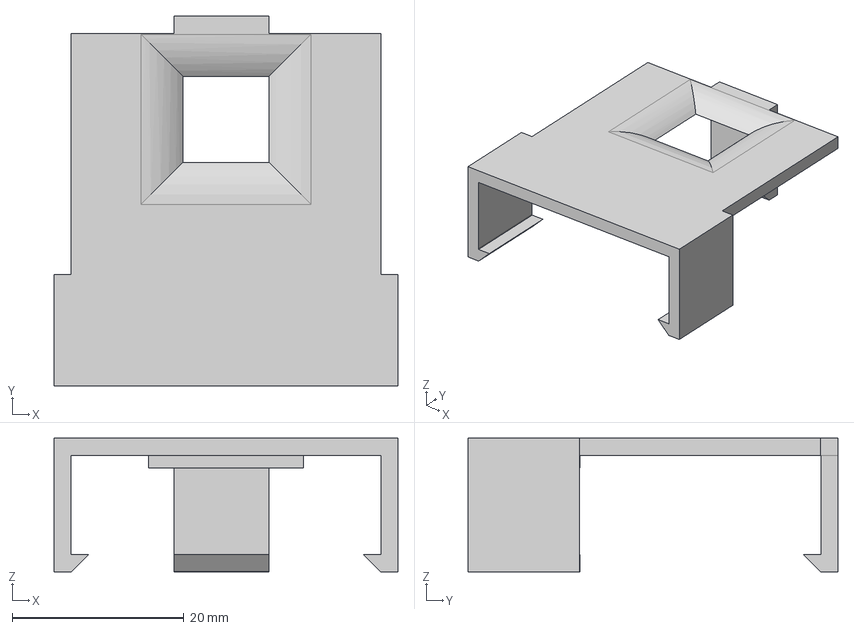
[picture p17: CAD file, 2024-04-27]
Open AIR Sensors/Open AIR Sensor Housing/Duco Sensor Housing/Open_AIR_Sensor_Housing_Duco_Top_B.step
40.0 x 43.0 x 15.6 mm

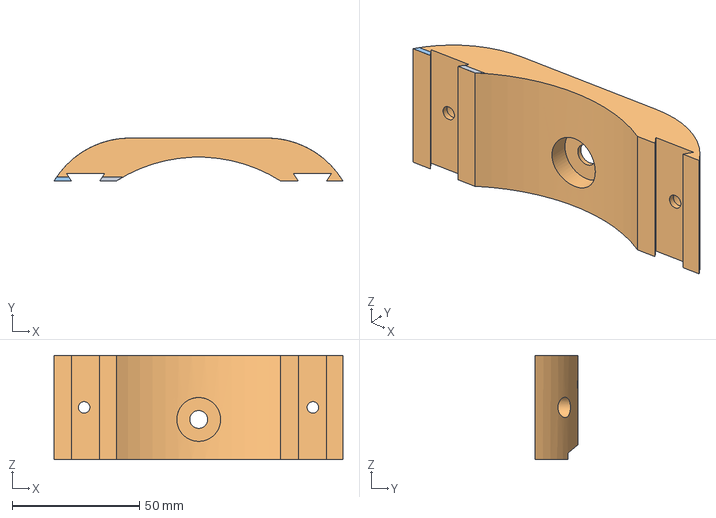
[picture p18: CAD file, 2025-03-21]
Open AIR Valve/Hardware/Open AIR Valve 3D prints/NEW (Hall Sensor)/Open_AIR_Valve_Bottom_C.step
113.4 x 16.9 x 40.9 mm

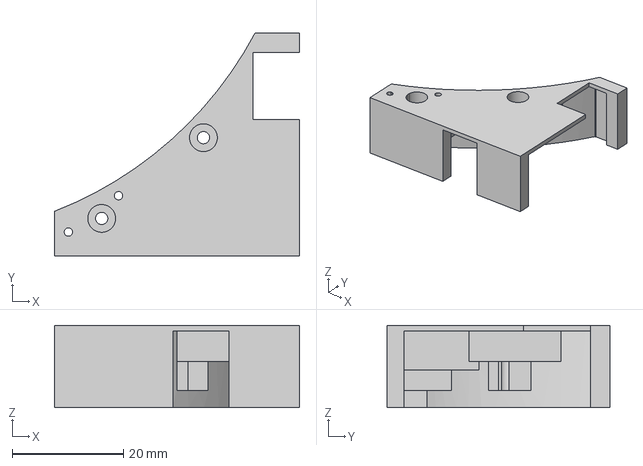
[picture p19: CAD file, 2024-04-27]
Open AIR Valve_External/Hardware/Open AIR Valve 3D prints/Open_AIR_Valve_External_PSU_Housing_A.step
44.0 x 40.0 x 14.8 mm

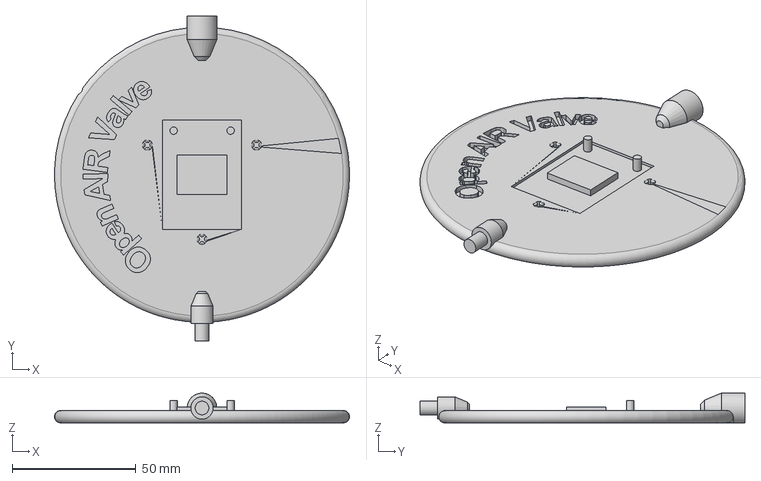
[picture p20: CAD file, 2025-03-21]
Open AIR Valve/Hardware/Open AIR Valve 3D prints/NEW (Hall Sensor)/Open_AIR_Valve_Disc_C.step
119.0 x 131.0 x 12.0 mm

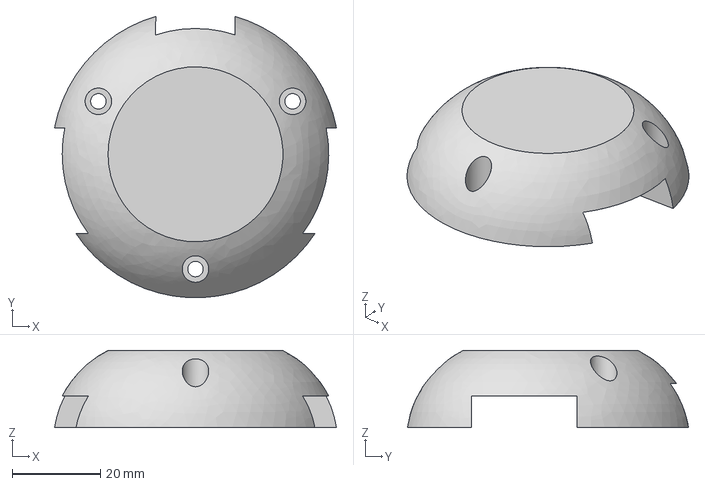
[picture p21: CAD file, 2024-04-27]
Open AIR Valve/Hardware/Open AIR Valve 3D prints/NEW (Hall Sensor)/Open_AIR_Valve_Sensor_Housing_A.step
63.9 x 63.7 x 17.5 mm

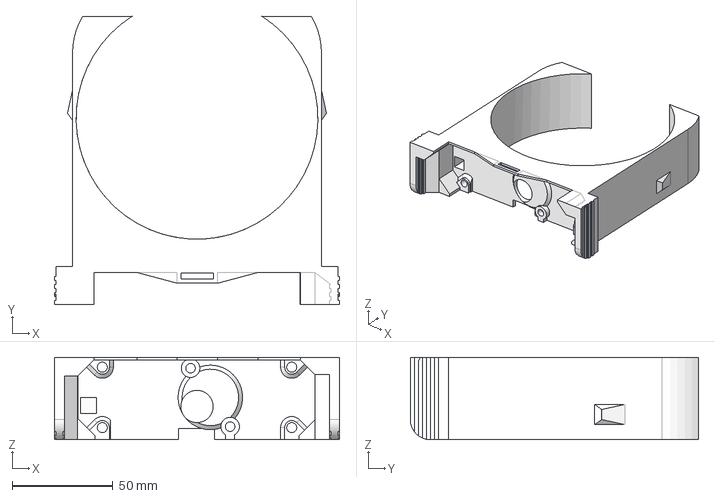
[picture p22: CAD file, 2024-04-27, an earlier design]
Open AIR Valve/Hardware/Open AIR Valve 3D prints/OLD (Omron Switch)/Open_AIR_Valve_Top_B.step
141.4 x 143.1 x 40.9 mm

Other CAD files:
Open AIR Valve/Hardware/Open AIR Valve 3D prints/OLD (Omron Switch)/Open_AIR_Valve_Bottom_A.step
Open AIR Valve/Hardware/Open AIR Valve 3D prints/OLD (Omron Switch)/Open_AIR_Valve_Disc_A.step

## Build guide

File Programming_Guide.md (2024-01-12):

# Programming Guide for Open AIR Devices

This guide provides detailed instructions for programming Open AIR Devices. There are three primary methods:

1. UART Programming.
2. OTA (Over-The-Air) from ESPHome.
3. OTA from a Web Browser.

**Warning**: Incorrect configurations can disable options 2 and 3. Exercise caution when applying custom YAML configurations.

## Option 1: UART Programming
To begin programming with UART, ESPHome needs to be installed on your computer or within Home Assistant (HA).

### Step 1: Install Python
- **Download Python for Windows**: Visit the [Windows Python Download Page](https://www.python.org/downloads/windows).
- **Installation**: Choose the latest Windows installer version (e.g., 3.9.9 64-bit). Ensure to select 'Add Python to PATH' during installation for easier command execution.

  Python Installer

  After installation, you should see a screen confirming the successful installation.

  Installation Success

### Step 2: Install ESPHome
- **Open Command Prompt**: Search for 'CMD' in the start menu, then press Enter or click the Command Prompt app.
- **Install Command**: In the Command Prompt, type `pip3 install esphome` and press Enter. Wait for the installation process to complete.

  ESPhome Installation

### Step 3: Connect Your Open AIR Device 

To connect your Open AIR Device, you have two options:
- Use an Open AIR Programmer.
- Use a 3.3V compatible USB-UART bridge.

Refer to the pinout diagram here: [Pinout Diagram](https://github.com/Flamingo-tech/Open-AIR/blob/main/Open%20AIR%20Valve/Hardware/Open%20AIR%20Valve%20PCB%20Overview_A.pdf)

All Open AIR Devices use the same pinout on the UART Debug Port.

### Step 4: Upload 

1. **Uploading Firmware**: 
   - Open the Command Prompt.
   - Type the command `esphome run YOURCONFIG.yaml` (replace `YOURCONFIG.yaml` with your configuration file name).
   - Press Enter to start the process. 

   Note: The compilation might take some time.

2. **Selecting Upload Option**: 
   - After compilation, choose the appropriate upload option as shown below:
     
     Upload Option

   - Press the number corresponding to the correct COM port option, followed by Enter.

3. **Important Steps During Upload**: 
   - When the message "connecting" appears, press the program button on the Open AIR Device.
   - While holding the program button, press the Reset button once.

   Following these steps will initiate the uploading process.

## Option 2: OTA (Over-The-Air) from ESPHome

Follow the Option 1 Esphome installation tutorial.

1. **Uploading Firmware**: 
   - Open the Command Prompt.
   - Type the command `esphome upload YOURCONFIG.yaml --device IP_OF_YOUR_DEVICE` 
     - Replace `YOURCONFIG.yaml` with your configuration file name.
     - Replace `IP_OF_YOUR_DEVICE` with your Open AIR device IP address.
     - Sometimes it will ask for an OTA password. By default, this is: `9f2ab9aa715f573e2476e75a5ec7f4e7`.      		
   - Press Enter to start the process. 

## Option 3: OTA (Over-The-Air) from the browser

Follow the Option 1 Esphome installation tutorial.

1. **Uploading Firmware**: 
   - Open your browser.
   - Navigate to the IP of your Open AIR Device, for example: `192.168.1.217`.
   - On the bottom of the page page is an OTA upload button. Press it.
   - You need to navigate to a binary generated by ESPHome. The easiest way to find it:
     - Open the Command Prompt.
     - Type the command `esphome run YOURCONFIG.yaml` (replace `YOURCONFIG.yaml` with your configuration file name).
     - Press Enter to start the process. 
     - When this process is finished, it will ask you how to upload the compiled binary. However, just above the successfully compiled program line is your BIN file location.
   - Go back to your browser and navigate to the file path given by ESPHome. Select the correct binary and press upload.

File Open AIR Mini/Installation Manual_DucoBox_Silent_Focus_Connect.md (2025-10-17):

 # Easy installation Manual For Open AIR Mini in Duco Systems

 **Special thanks to D.Smith for helping and inspiring me for writing this :)!**

 This guide assumes you've chosen the **pre-programmed** option when you've bought the Open AIR Mini. This guide will guide you trough the installation/Home Assistant proces.

 ## Introduction

The Open Air Mini is an innovative electronic circuit intended to replace the existing circuitry in your ventilation box. It is a product of an open-source endeavor aimed at giving you the power to control your preferred mechanical ventilation unit through your home automation system.

Typically, ventilation boxes, like those from DUCO or ORCON, can have their circuit boards upgraded with the Open Air Mini. This modification enables you to control your ventilation using a home automation system or even through a web browser.

The typical use case is to implement demand-driven ventilation. This system measures air quality factors such as CO2 and moisture. Based on these measurements, it adjusts the ventilation in your home. Consequently, it promotes energy efficiency by pausing the ventilation system's motor when not needed, and preventing the unnecessary expulsion of warm air from your home.

The Open Air Mini not only contributes to energy-saving but also provides freedom from vendor lock-in. It operates independently of cloud services and ensures your statistics remain private. It's a perfect blend of convenience, efficiency, and privacy.

**Important Notice**
Please be aware that this project operates independently and does not have support or affiliation with Duco, Orcon, or any other vendor. Moreover, there is no technical assistance available from these companies. If you choose to modify your ventilation box using the Open Air Mini, it is a decision made solely at your discretion and assumed risk. Remember, undertaking modifications implies accepting full responsibility for any potential consequences.

 ## Installation in a Ducobox Silent

 The installation proces is done in 7 easy steps!

 1. Locating Your Docubox Silent
 2. Remove Power
 3. Remove Original Hardware
 4. Insert Open AIR Mini
 5. Connect your Open AIR Mini
 6. Powering up Your Open AIR Mini
 7. Adding the Open AIR Mini to Home Assistant

# 1 Locating Your Docubox Silent

The location of your ventilation box can vary within your home. We encourage you to locate it. As a homeowner, this task should be straightforward and can be quite an enlightening step in familiarizing yourself further with your home's infrastructure. ;)
Please remove the white cover. You will be greated with:
<p align="center">
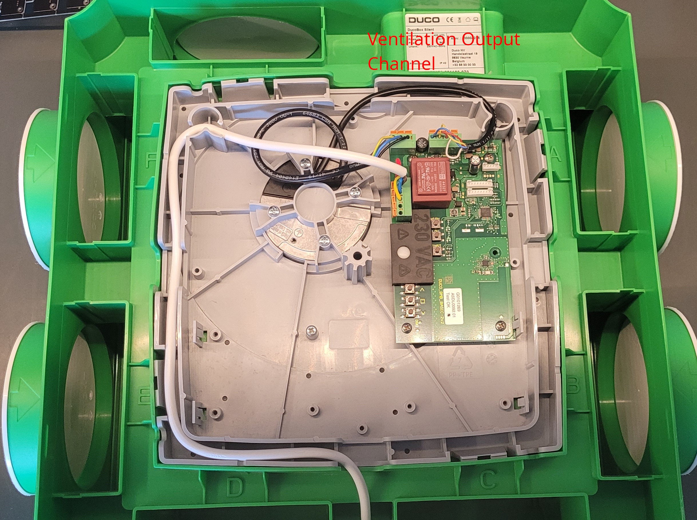
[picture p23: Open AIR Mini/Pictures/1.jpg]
  
</p>

# 2 Remove Power

It is critical to disconnect your Ducobox Silent before proceeding. This step is extremely important. **Neglecting to do so could result in severe injury or even death. Make sure to cut off all power supply.**

Ensure, then doubly ensure, that you've disconnected the correct plug. It's better to check multiple times than risk an accident.

If you're unsure about any aspect of these steps or find them confusing, don't hesitate to seek help. You might ask someone who's more familiar with the process, or consider hiring a professional. Safety should always be your top priority.
<p align="center">
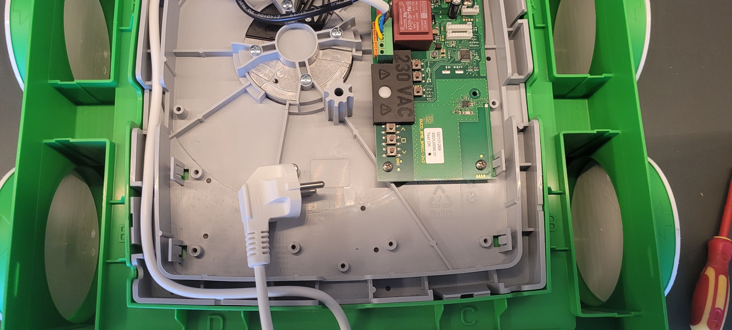
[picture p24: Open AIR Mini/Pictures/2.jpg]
  
</p>

Proceed to detach the cables from the original Ducobox hardware:
Press on the orange tabs (highlighted in red in the image provided) and gently pull the wires out from their respective connectors.
<p align="center">
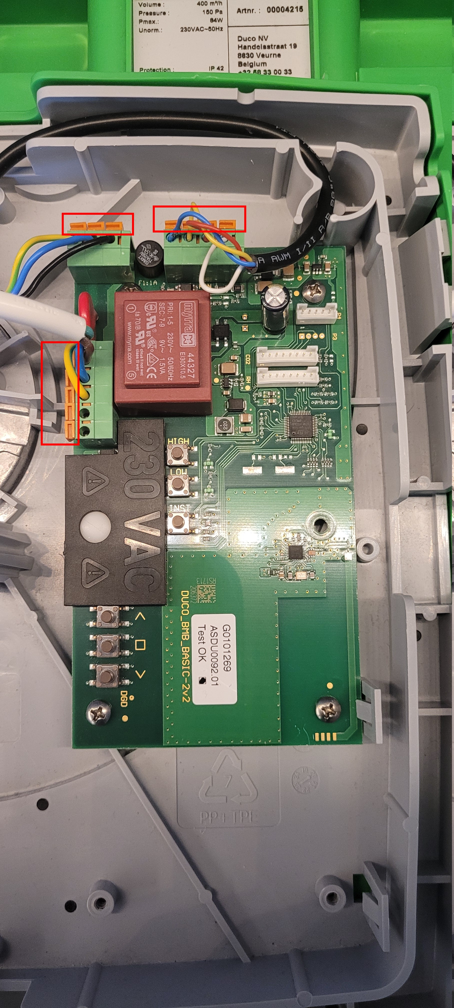
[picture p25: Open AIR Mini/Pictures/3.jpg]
  
</p>

When done it should look like this:
<p align="center">
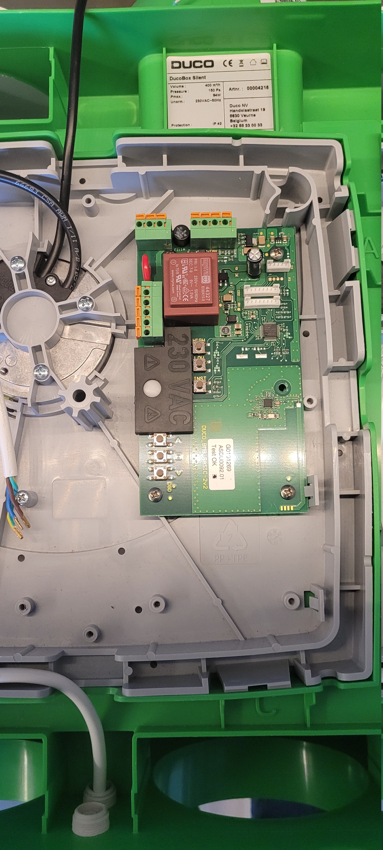
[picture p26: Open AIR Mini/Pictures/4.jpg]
  
</p>

# 3. Remove Original Hardware

Please use a screwdriver to carefully remove the four screws indicated in red in the image provided.
<p align="center">
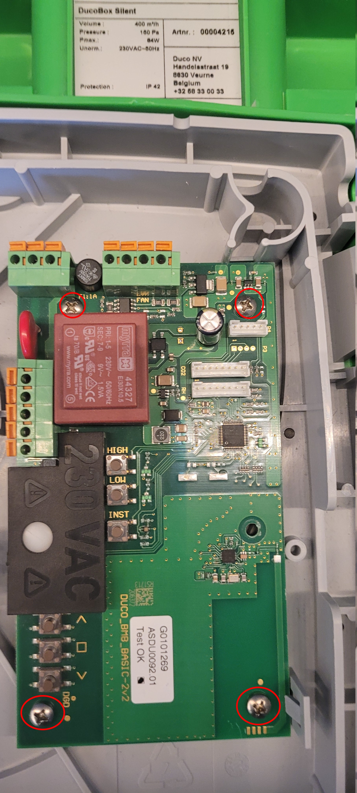
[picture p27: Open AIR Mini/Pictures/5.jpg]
  
</p>

Be sure to safely store the original circuit board after removal. If you ever decide to sell or rent your house in the future, you'll have the option to reinstall the original Duco hardware. Its availability will provide flexibility for future circumstances.

# 4. Insert Open AIR Mini

For the installation of the Open AIR Mini, position it as follows:
<p align="center">
  
</p>

Proceed to secure the Open AIR Mini by reinstalling the screws into the locations indicated in red:
<p align="center">
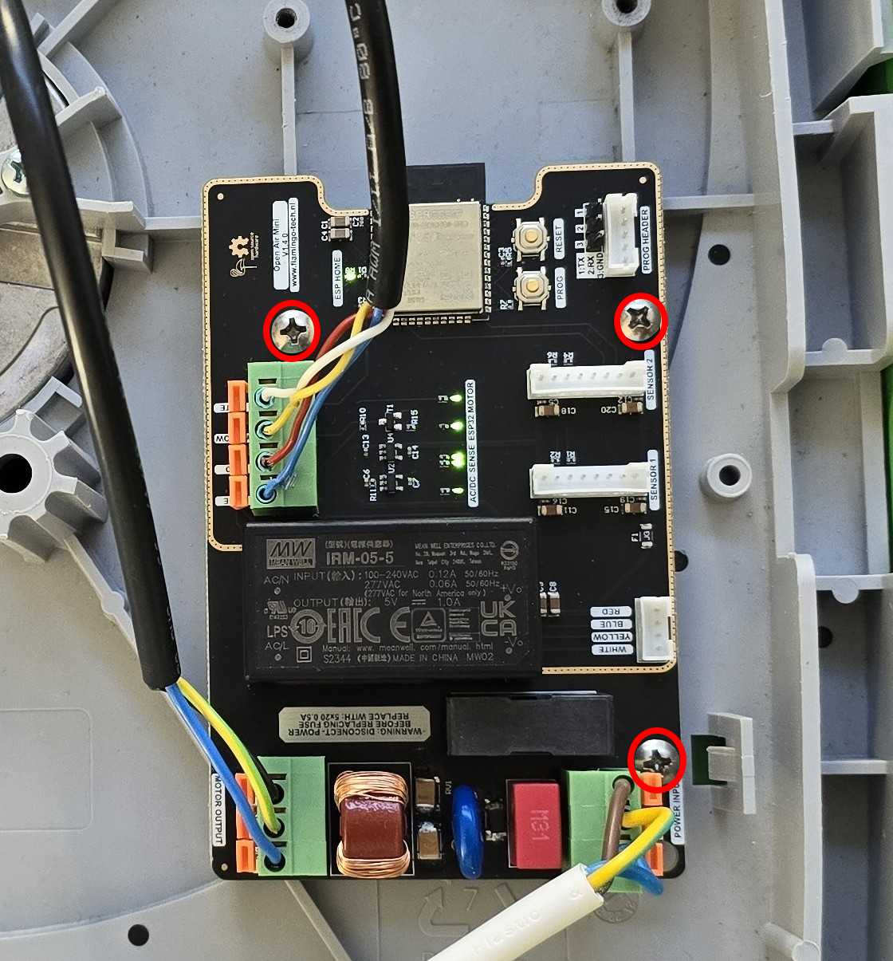
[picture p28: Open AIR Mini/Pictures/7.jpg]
  
</p>

# 5. Connect your Open AIR Mini

To provide power to your Open Air Mini, you'll need to connect the power cable to the bottom connector, which is colored green. **This is a crucial step: Press the orange tab and insert the cable simultaneously to ensure a solid connection.**

This process involves pushing the cable in as far as it will go. Once the cable is fully inserted, release the orange tab. Finally, give the cable a gentle pull to confirm it's securely connected. It's essential that the connection is firm to ensure proper operation.

<p align="center">
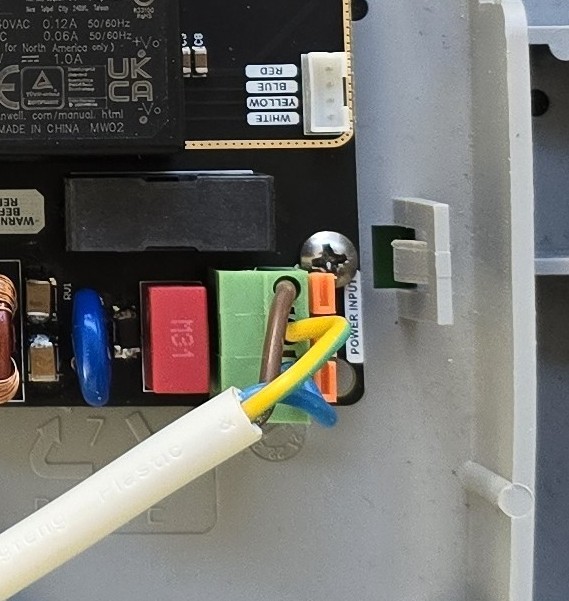
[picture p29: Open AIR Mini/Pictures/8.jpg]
  
</p>

Please pay close attention to the sequence in which the cables need to be connected!

After this connect the motor power:

<p align="center">
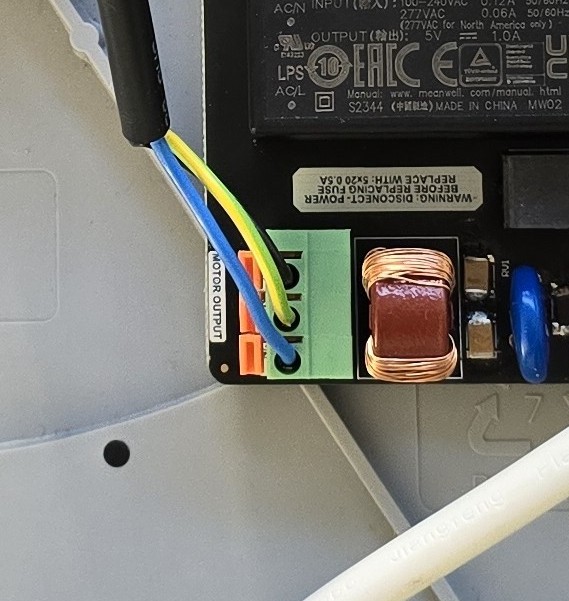
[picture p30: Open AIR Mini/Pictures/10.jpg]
  
</p>

Please pay close attention to the sequence in which the cables need to be connected!

Now connect the motor data cable:

<p align="center">
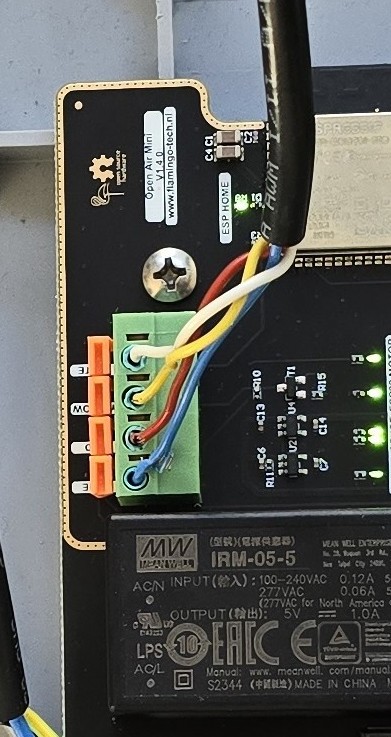
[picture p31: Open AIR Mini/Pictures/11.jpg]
  
</p>

Please pay close attention to the sequence in which the cables need to be connected!

Once all the cables are connected, make it a point to give each of them a gentle pull. This is to doubly ensure that they are firmly and correctly connected, providing a secure foundation for optimal operation.

# 6. Powering up Your Open AIR Mini

Reconnect the power plug to your Ducobox. You should now see a multitude of green LEDs light up.
Ensure that all five LEDs at the top of the circuit board are illuminated. If any of them are not on, please reach out to me at flamingo-tech@protonmail.com for assistance.
If you have the **pre-programmed option**, the ESPHome LED (marked by the lower green LED) should be blinking.
<p align="center">
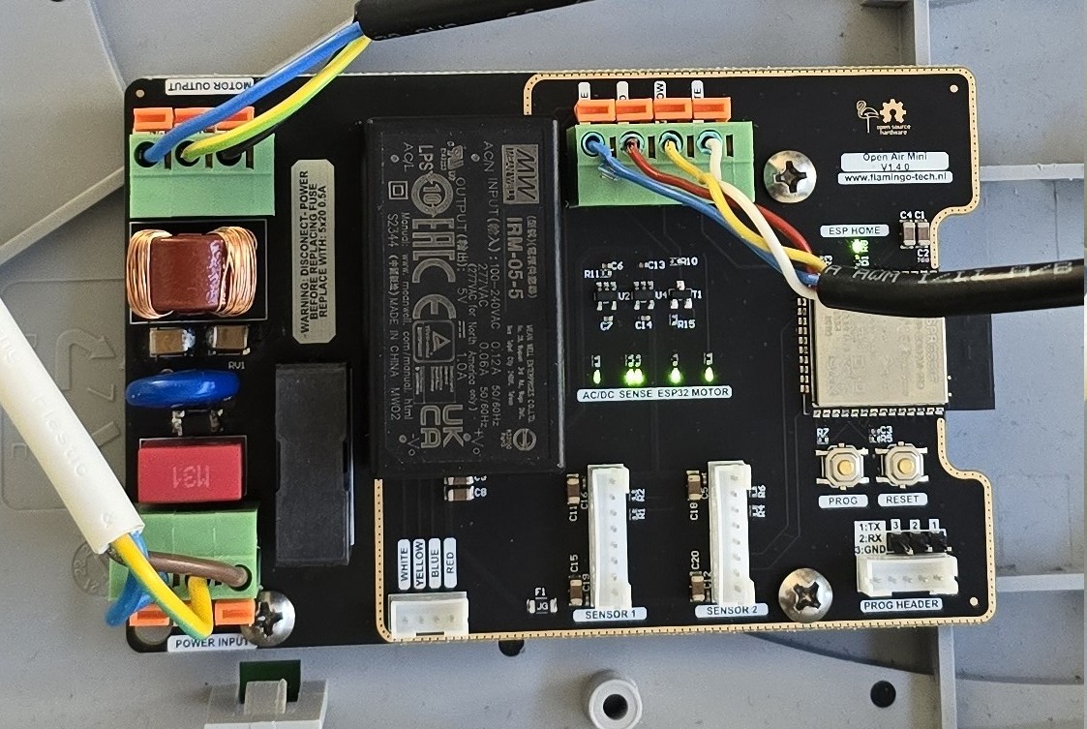
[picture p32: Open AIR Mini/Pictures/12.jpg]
  
</p>

Now you can finally close the ventilation box.

# 7. Adding the Open AIR Mini to Home Assistant

Now open your home assistant page.
If this is the first time using a ESPHOME device:
Go to settings -> Integrations -> Set up a new integration -> Search for esphome.
Now click the esphome intergration and fill in the IP adress of the Home Assistant server. 

Use your mobile phone and or laptop for this step. Please connect to the following network: "Open-AIR-Mini Fallback"
Use this password: "ChangeMe@123!"
Once you've successfully connected to the fallback hotspot using your phone or laptop, opening your browser should direct you to a landing page where you can establish your own network.
If you don't automatically land on this page, you can manually navigate to it by entering the following URL: http://192.168.4.1 in the browser and navigate to it.
Upon reaching this page, you should be greeted with a screen that resembles the following:
<p align="center">
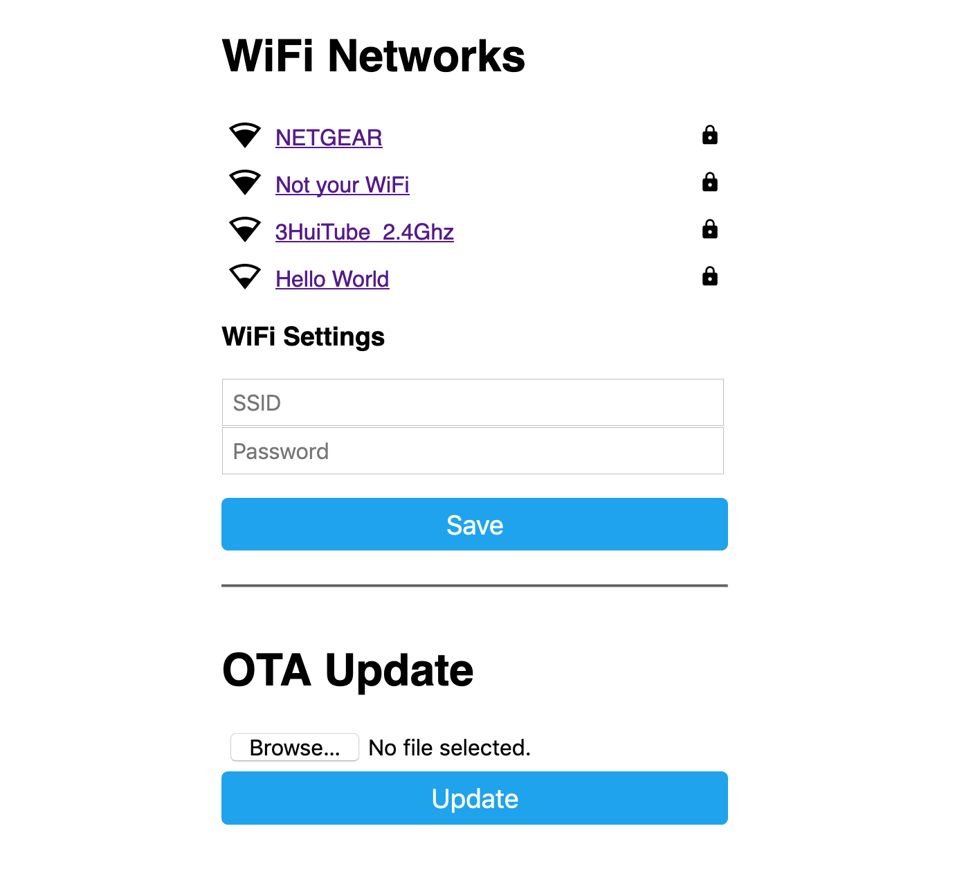
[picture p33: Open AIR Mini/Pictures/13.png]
  
</p>

Next, select your network and input your credentials. After this step, the device will undergo a reboot process, which may take approximately 4-5 minutes. Once completed, you should be able to see your Home Assistant (HA) environment directly, ensuring a smooth setup process.

Should you encounter any difficulties and the process fails for some reason, you have the option to manually reset the device using the reset button. If the fallback hotspot reappears, this suggests that the Open AIR Mini was unable to establish a connection with your network. In such a case, please attempt the process again.

It's worth noting that if you're utilizing a hidden SSID you cant use the pre-programmed option!

Upon successful completion of these steps, your Home Assistant should generate a "New Devices Discovered" notification. To proceed, click on the "Check it Out" option, then select the "Configure" button on the new ESPHome device. A pop-up window should appear next; hit the "Submit" button.

If HA asks for an encryption key use:"YCZELYrS1Di6tDmWNDSFRVaXJEYG9RxAldRHNPXXt3o="

Congratulations, you're all set! You can now begin creating custom automations for your device. Enjoy exploring the possibilities this brings to your home environment.

**After adding the Open AIR Mini to a dashboard long press the fan logo and then you can change the RPM**

Have fun :)

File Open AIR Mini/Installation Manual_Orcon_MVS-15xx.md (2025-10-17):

 # Easy installation Manual For Open AIR Mini for Orcon MVS-15xx

 **Special thanks to D.Smith for helping and inspiring me for writing this :)!**

 This guide assumes you've chosen the **pre-programmed** option when you've bought the Open AIR Mini. This guide will guide you trough the installation/Home Assistant proces.

 ## Introduction

The Open Air Mini is an innovative electronic circuit intended to replace the existing circuitry in your ventilation box. It is a product of an open-source endeavor aimed at giving you the power to control your preferred mechanical ventilation unit through your home automation system.

Typically, ventilation boxes, like those from DUCO or ORCON, can have their circuit boards upgraded with the Open Air Mini. This modification enables you to control your ventilation using a home automation system or even through a web browser.

The typical use case is to implement demand-driven ventilation. This system measures air quality factors such as CO2 and moisture. Based on these measurements, it adjusts the ventilation in your home. Consequently, it promotes energy efficiency by pausing the ventilation system's motor when not needed, and preventing the unnecessary expulsion of warm air from your home.

The Open Air Mini not only contributes to energy-saving but also provides freedom from vendor lock-in. It operates independently of cloud services and ensures your statistics remain private. It's a perfect blend of convenience, efficiency, and privacy.

**Important Notice**
Please be aware that this project operates independently and does not have support or affiliation with Duco, Orcon, or any other vendor. Moreover, there is no technical assistance available from these companies. If you choose to modify your ventilation box using the Open Air Mini, it is a decision made solely at your discretion and assumed risk. Remember, undertaking modifications implies accepting full responsibility for any potential consequences.

 ## Installation in a Orcon MVS-15xx

 The installation proces is done in 7 easy steps!

 1. Locating Your Orcon MVS-15xx
 2. Remove Power
 3. Remove Original Hardware
 4. Insert Open AIR Mini
 5. Connect your Open AIR Mini
 6. Powering up Your Open AIR Mini
 7. Adding the Open AIR Mini to Home Assistant

# 1 Locating Your MVS-15xx Silent

The location of your ventilation box can vary within your home. We encourage you to locate it. As a homeowner, this task should be straightforward and can be quite an enlightening step in familiarizing yourself further with your home's infrastructure. ;)
Please remove the white cover. You will be greated with:
<p align="center">
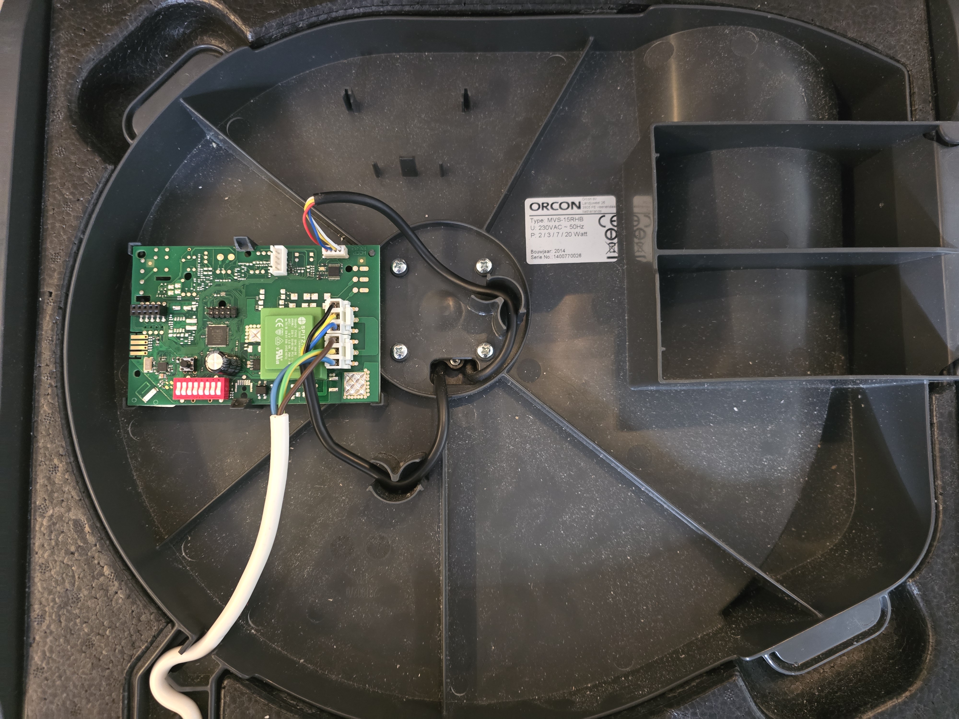
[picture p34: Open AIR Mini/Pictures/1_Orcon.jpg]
  
</p>

The cover may prove challenging to detach as it is secured by four semi-circular white components (on the sides of the box). I managed to wedge a screwdriver beneath these parts. This action revealed the inner workings of Orcon ventilation box.

# 2 Remove Power

It is critical to disconnect your Orcon ventilation before proceeding. This step is extremely important. **Neglecting to do so could result in severe injury or even death. Make sure to cut off all power supply.**

Ensure, then doubly ensure, that you've disconnected the correct plug. It's better to check multiple times than risk an accident.

If you're unsure about any aspect of these steps or find them confusing, don't hesitate to seek help. You might ask someone who's more familiar with the process, or consider hiring a professional. Safety should always be your top priority.

Proceed to detach the cables from the original Orcon hardware:
For the two big connectors you need to pinch the white tab. For the smaller four pin connector, just pull.
<p align="center">
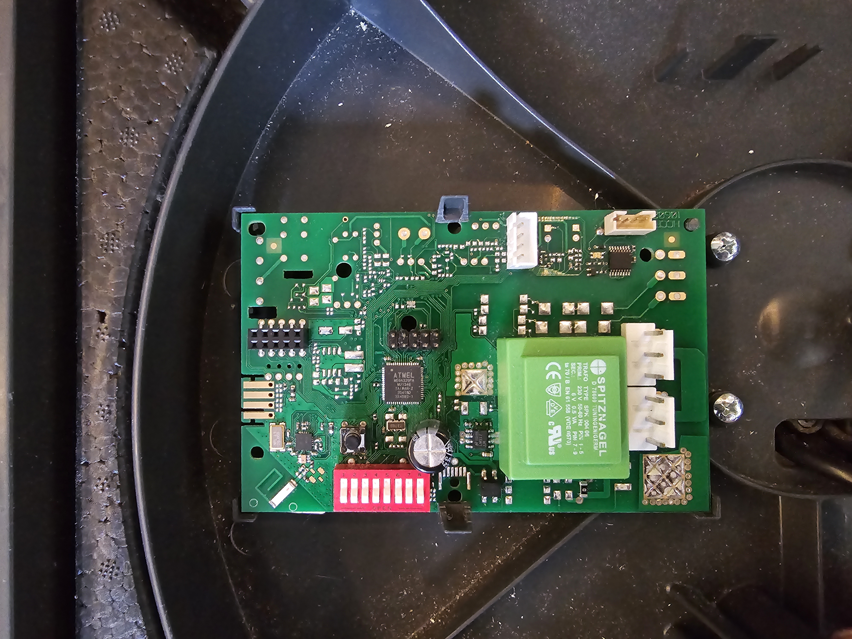
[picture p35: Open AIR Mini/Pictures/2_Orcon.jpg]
  
</p>

# 3. Remove Original Hardware

Push the two tabs on the side, and pull the board up. It should lift right up.
<p align="center">
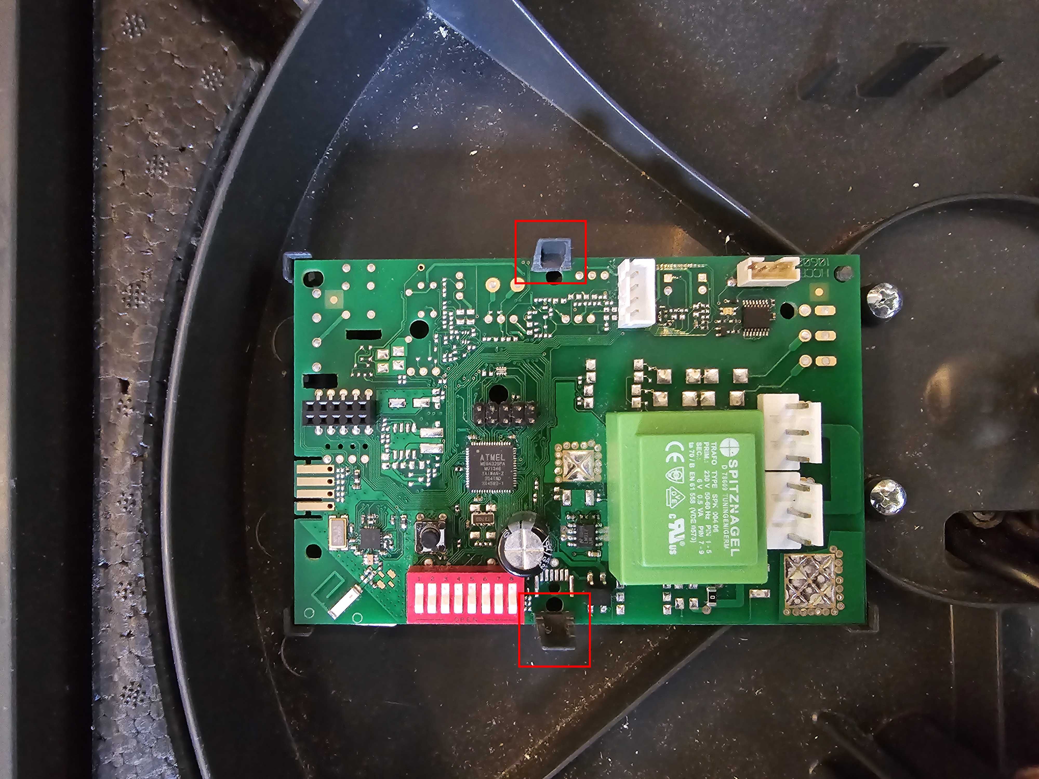
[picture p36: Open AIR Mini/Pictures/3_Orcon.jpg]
  
</p>

Be sure to safely store the original circuit board after removal. If you ever decide to sell or rent your house in the future, you'll have the option to reinstall the original Orcon hardware. Its availability will provide flexibility for future circumstances.

# 4. Insert Open AIR Mini

For the installation of the Open AIR Mini, position it as follows:
<p align="center">
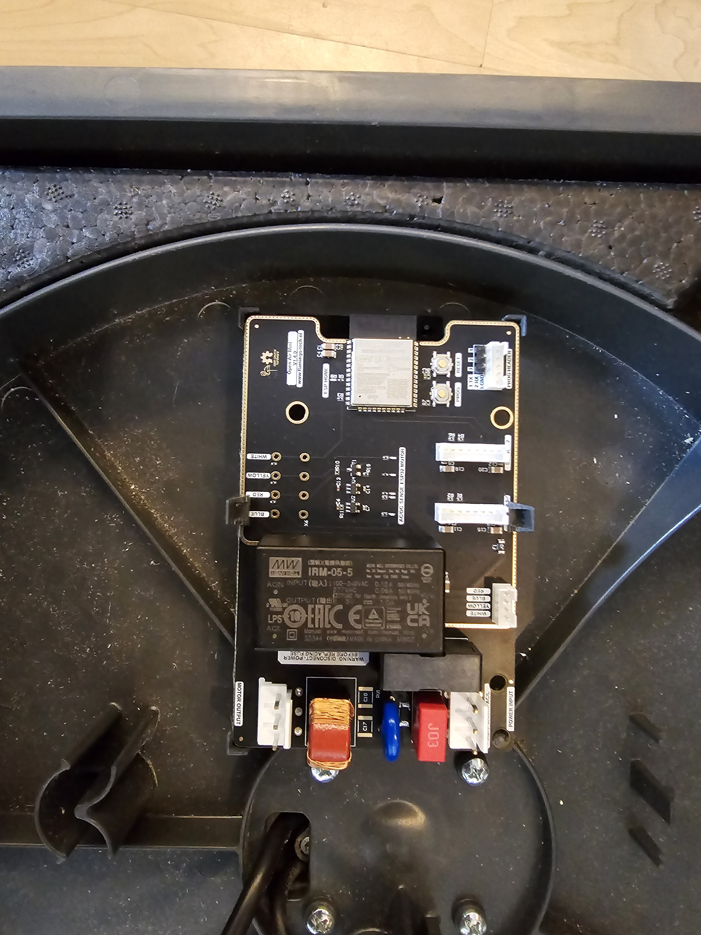
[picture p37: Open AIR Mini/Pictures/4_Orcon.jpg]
  
</p>

Gently pull the tabs to the side again and slide the Open AIR Mini in place.

# 5. Connect your Open AIR Mini

To provide power to your Open Air Mini, you'll need to connect the power cable to the white connector labled "Power Input". 
To provide power to your Orcon Motor, you'll need to connect the power cable to the white connector labled "Motor Output". 

Please pay close attention to the sequence in which the cables need to be connected:
<p align="center">
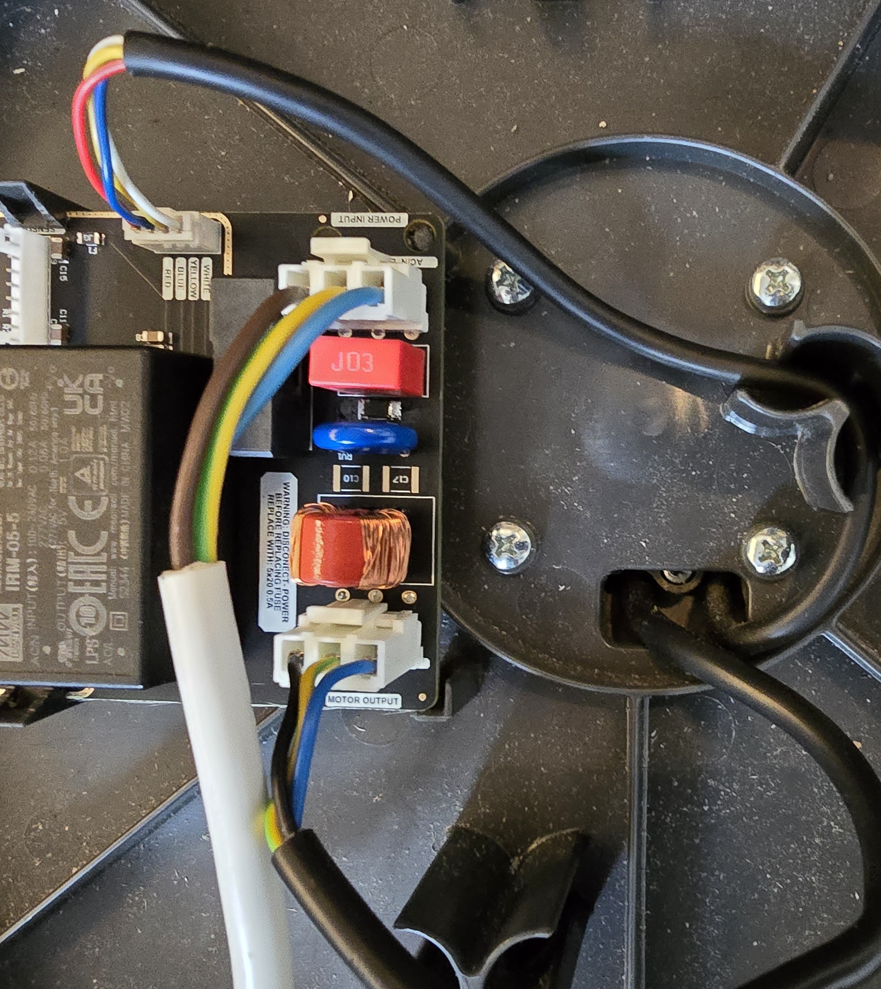
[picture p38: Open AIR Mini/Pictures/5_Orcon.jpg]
  
</p>

Once all the cables are connected, make it a point to give each of them a gentle pull. This is to doubly ensure that they are firmly and correctly connected, providing a secure foundation for optimal operation.

# 6. Powering up Your Open AIR Mini

Reconnect the power plug to your Orcon box. You should now see a multitude of green LEDs light up.
Ensure that all five LEDs at the top of the circuit board are illuminated. If any of them are not on, please reach out to me at flamingo-tech@protonmail.com for assistance.
If you have the **pre-programmed option**, the ESPHome LED (marked by the lower green LED) should be blinking.

Now you can finally close the ventilation box.

# 7. Adding the Open AIR Mini to Home Assistant

Now open your home assistant page.
If this is the first time using a ESPHOME device:
Go to settings -> Integrations -> Set up a new integration -> Search for esphome.
Now click the esphome intergration and fill in the IP adress of the Home Assistant server. 

Use your mobile phone and or laptop for this step. Please connect to the following network: "Open-AIR-Mini Fallback"
Use this password: "ChangeMe@123!"
Once you've successfully connected to the fallback hotspot using your phone or laptop, opening your browser should direct you to a landing page where you can establish your own network.
If you don't automatically land on this page, you can manually navigate to it by entering the following URL: http://192.168.4.1 in the browser and navigate to it.
Upon reaching this page, you should be greeted with a screen that resembles the following:
<p align="center">
  
</p>

Next, select your network and input your credentials. After this step, the device will undergo a reboot process, which may take approximately 4-5 minutes. Once completed, you should be able to see your Home Assistant (HA) environment directly, ensuring a smooth setup process.

Should you encounter any difficulties and the process fails for some reason, you have the option to manually reset the device using the reset button. If the fallback hotspot reappears, this suggests that the Open AIR Mini was unable to establish a connection with your network. In such a case, please attempt the process again.

It's worth noting that if you're utilizing a hidden SSID you cant use the pre-programmed option!

Upon successful completion of these steps, your Home Assistant should generate a "New Devices Discovered" notification. To proceed, click on the "Check it Out" option, then select the "Configure" button on the new ESPHome device. A pop-up window should appear next; hit the "Submit" button.

If HA asks for an encryption key use:"YCZELYrS1Di6tDmWNDSFRVaXJEYG9RxAldRHNPXXt3o="

Congratulations, you're all set! You can now begin creating custom automations for your device. Enjoy exploring the possibilities this brings to your home environment.

**After adding the Open AIR Mini to a dashboard long press the fan logo and then you can change the RPM**

Have fun :)

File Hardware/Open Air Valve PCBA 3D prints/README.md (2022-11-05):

# Open_Air
Open source system for home ventilation and control via HA

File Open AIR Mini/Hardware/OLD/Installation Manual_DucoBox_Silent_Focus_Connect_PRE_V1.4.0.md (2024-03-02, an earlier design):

 # Easy installation Manual For Open AIR Mini

 **Special thanks to D.Smith for helping and inspiring me for writing this :)!**

 This guide assumes you've chosen the **pre-programmed** option when you've bought the Open AIR Mini. This guide will guide you trough the installation/Home Assistant proces.

 ## Introduction

The Open Air Mini is an innovative electronic circuit intended to replace the existing circuitry in your ventilation box. It is a product of an open-source endeavor aimed at giving you the power to control your preferred mechanical ventilation unit through your home automation system.

Typically, ventilation boxes, like those from DUCO or ORCON, can have their circuit boards upgraded with the Open Air Mini. This modification enables you to control your ventilation using a home automation system or even through a web browser.

The typical use case is to implement demand-driven ventilation. This system measures air quality factors such as CO2 and moisture. Based on these measurements, it adjusts the ventilation in your home. Consequently, it promotes energy efficiency by pausing the ventilation system's motor when not needed, and preventing the unnecessary expulsion of warm air from your home.

The Open Air Mini not only contributes to energy-saving but also provides freedom from vendor lock-in. It operates independently of cloud services and ensures your statistics remain private. It's a perfect blend of convenience, efficiency, and privacy.

**Important Notice**
Please be aware that this project operates independently and does not have support or affiliation with Duco, Orcon, or any other vendor. Moreover, there is no technical assistance available from these companies. If you choose to modify your ventilation box using the Open Air Mini, it is a decision made solely at your discretion and assumed risk. Remember, undertaking modifications implies accepting full responsibility for any potential consequences.

 ## Installation in a Ducobox Silent

 The installation proces is done in 7 easy steps!

 1. Locating Your Docubox Silent
 2. Remove Power
 3. Remove Original Hardware
 4. Insert Open AIR Mini
 5. Connect your Open AIR Mini
 6. Powering up Your Open AIR Mini
 7. Adding the Open AIR Mini to Home Assistant

# 1 Locating Your Docubox Silent

The location of your ventilation box can vary within your home. We encourage you to locate it. As a homeowner, this task should be straightforward and can be quite an enlightening step in familiarizing yourself further with your home's infrastructure. ;)
Please remove the white cover. You will be greated with:


# 2 Remove Power

It is critical to disconnect your Ducobox Silent before proceeding. This step is extremely important. **Neglecting to do so could result in severe injury or even death. Make sure to cut off all power supply.**

Ensure, then doubly ensure, that you've disconnected the correct plug. It's better to check multiple times than risk an accident.

If you're unsure about any aspect of these steps or find them confusing, don't hesitate to seek help. You might ask someone who's more familiar with the process, or consider hiring a professional. Safety should always be your top priority.


Proceed to detach the cables from the original Ducobox hardware:
Press on the orange tabs (highlighted in red in the image provided) and gently pull the wires out from their respective connectors.

When done it should look like this:


# 3. Remove Original Hardware

Please use a screwdriver to carefully remove the four screws indicated in red in the image provided.


Be sure to safely store the original circuit board after removal. If you ever decide to sell or rent your house in the future, you'll have the option to reinstall the original Duco hardware. Its availability will provide flexibility for future circumstances.

# 4. Insert Open AIR Mini

For the installation of the Open AIR Mini, position it as follows:
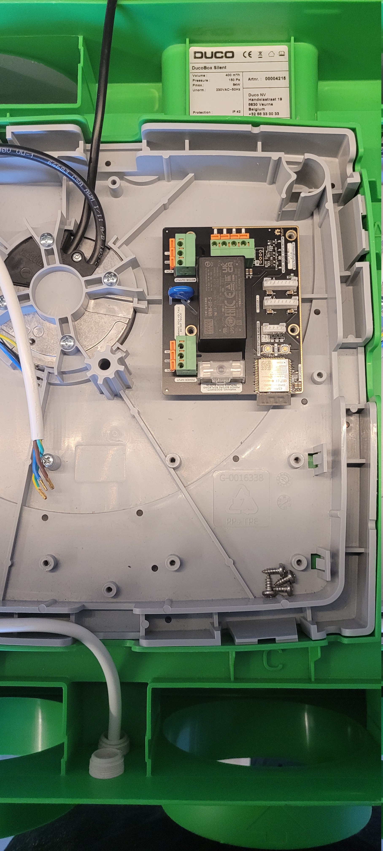
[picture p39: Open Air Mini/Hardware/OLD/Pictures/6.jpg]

Proceed to secure the Open AIR Mini by reinstalling the screws into the locations indicated in red:
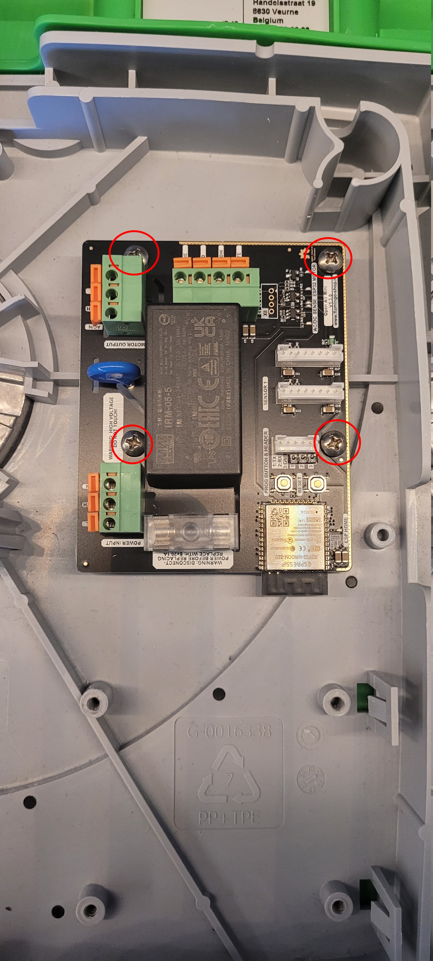
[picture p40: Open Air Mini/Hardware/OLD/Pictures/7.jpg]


# 5. Connect your Open AIR Mini

To provide power to your Open Air Mini, you'll need to connect the power cable to the bottom connector, which is colored green. **This is a crucial step: Press the orange tab and insert the cable simultaneously to ensure a solid connection.**

This process involves pushing the cable in as far as it will go. Once the cable is fully inserted, release the orange tab. Finally, give the cable a gentle pull to confirm it's securely connected. It's essential that the connection is firm to ensure proper operation.
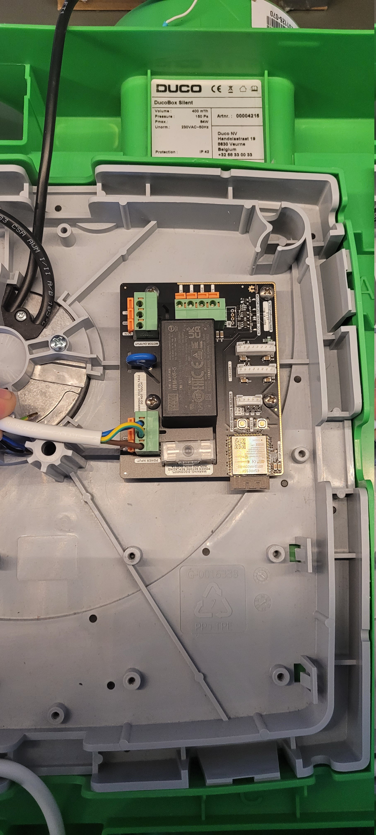
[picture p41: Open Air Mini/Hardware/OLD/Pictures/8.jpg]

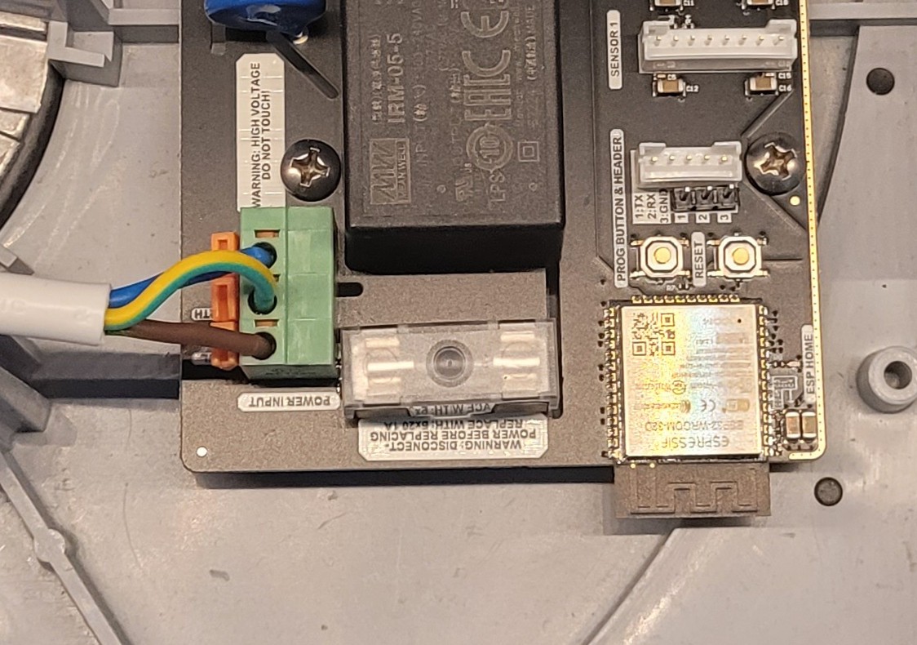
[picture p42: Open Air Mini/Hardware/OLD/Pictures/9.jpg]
Please pay close attention to the sequence in which the cables need to be connected:

After this connect the motor power:
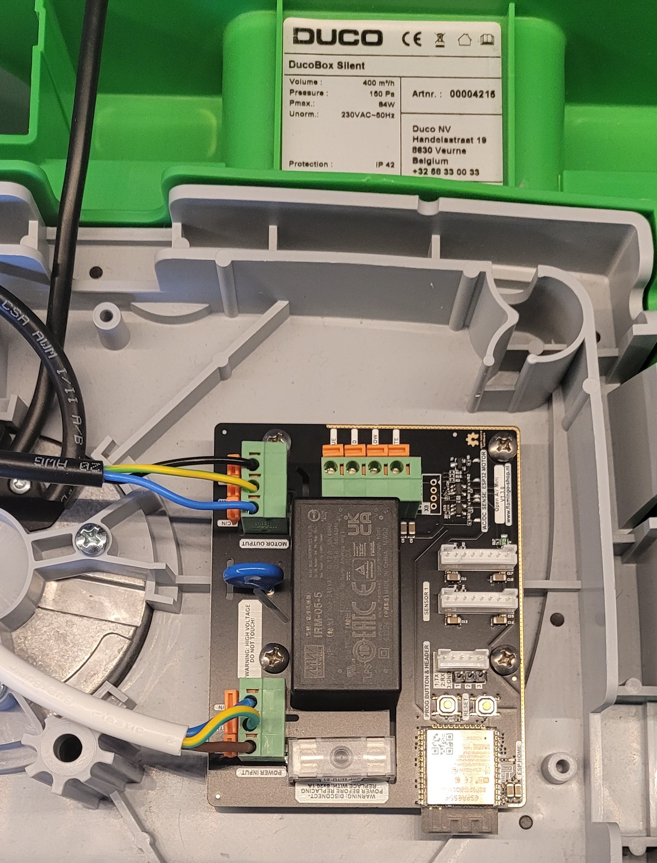
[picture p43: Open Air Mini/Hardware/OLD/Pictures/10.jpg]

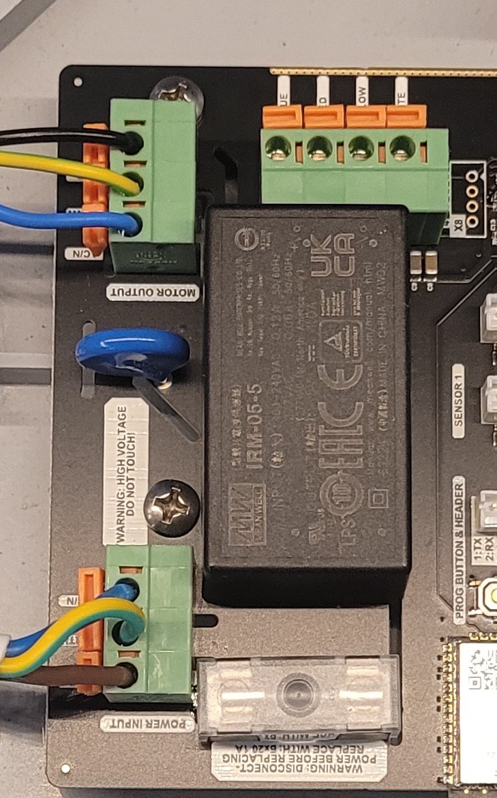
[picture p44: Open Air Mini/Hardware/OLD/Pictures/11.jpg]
Please pay close attention to the sequence in which the cables need to be connected:

Now connect the motor data cable:
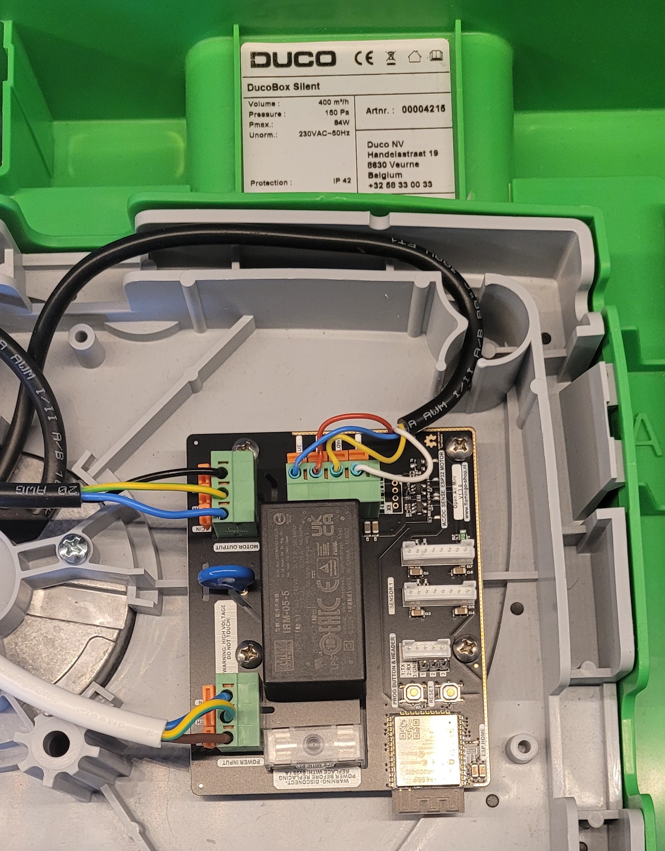
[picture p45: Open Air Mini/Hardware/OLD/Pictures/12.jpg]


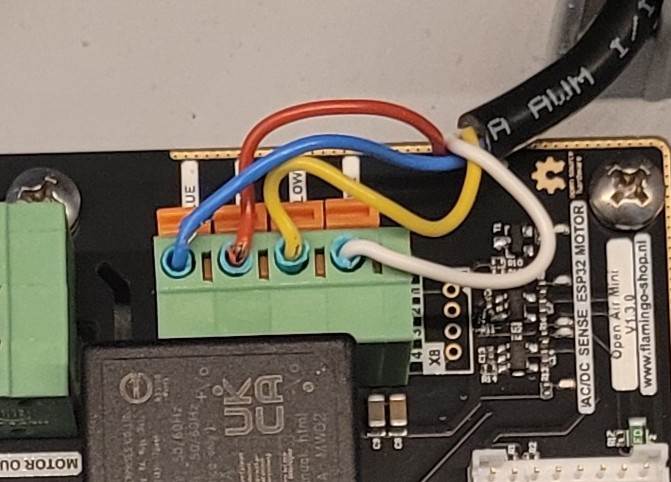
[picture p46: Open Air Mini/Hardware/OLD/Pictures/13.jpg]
Please pay close attention to the sequence in which the cables need to be connected:

Once all the cables are connected, make it a point to give each of them a gentle pull. This is to doubly ensure that they are firmly and correctly connected, providing a secure foundation for optimal operation.

# 6. Powering up Your Open AIR Mini

Reconnect the power plug to your Ducobox. You should now see a multitude of green LEDs light up.
Ensure that all five LEDs at the top of the circuit board are illuminated. If any of them are not on, please reach out to me at flamingo-tech@protonmail.com for assistance.
If you have the **pre-programmed option**, the ESPHome LED (marked by the lower green LED) should be blinking.
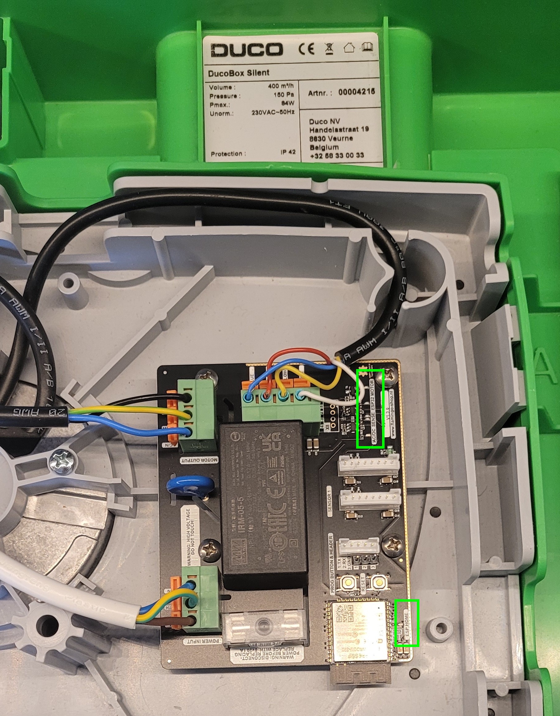
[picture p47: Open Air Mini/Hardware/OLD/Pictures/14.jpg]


Now you can finally close the ventilation box.

# 7. Adding the Open AIR Mini to Home Assistant

Now open your home assistant page.
If this is the first time using a ESPHOME device:
Go to settings -> Integrations -> Set up a new integration -> Search for esphome.
Now click the esphome intergration and fill in the IP adress of the Home Assistant server. 

Use your mobile phone and or laptop for this step. Please connect to the following network: "Open-AIR-Mini Fallback"
Use this password: "ChangeMe@123!"
Once you've successfully connected to the fallback hotspot using your phone or laptop, opening your browser should direct you to a landing page where you can establish your own network.
If you don't automatically land on this page, you can manually navigate to it by entering the following URL: http://192.168.4.1 in the browser and navigate to it.
Upon reaching this page, you should be greeted with a screen that resembles the following:

Next, select your network and input your credentials. After this step, the device will undergo a reboot process, which may take approximately 4-5 minutes. Once completed, you should be able to see your Home Assistant (HA) environment directly, ensuring a smooth setup process.

Should you encounter any difficulties and the process fails for some reason, you have the option to manually reset the device using the reset button. If the fallback hotspot reappears, this suggests that the Open AIR Mini was unable to establish a connection with your network. In such a case, please attempt the process again.

It's worth noting that if you're utilizing a hidden SSID you cant use the pre-programmed option!

Upon successful completion of these steps, your Home Assistant should generate a "New Devices Discovered" notification. To proceed, click on the "Check it Out" option, then select the "Configure" button on the new ESPHome device. A pop-up window should appear next; hit the "Submit" button.

Congratulations, you're all set! You can now begin creating custom automations for your device. Enjoy exploring the possibilities this brings to your home environment.

**After adding the Open AIR Mini to a dashboard long press the fan logo and then you can change the RPM**

Have fun :)

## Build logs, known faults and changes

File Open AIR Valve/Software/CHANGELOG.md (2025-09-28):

# Changelog

All notable changes to this project will be documented in this file.

The format is based on [Keep a Changelog](https://keepachangelog.com/en/1.0.0/),
and this project adheres to [Semantic Versioning](https://semver.org/spec/v2.0.0.html).

## [1.1.0]

### Changed

* Changed to Valve component instead of blinds <-- Will break automations!!
* Moved old config in OLD YAML folder

### Added

* Added support for ESPHOME Version: 2025.9.1
* Added ESP-IDF instead of Arduino framework
* Added Version to Diagnostic tab in HA
* Added MCU Temperature in diagnostic tab in HA
* Added Uptime to diagnostic tab in HA
* Added WiFi IP in diagnostic tab in HA
* Added Re-home button, no need to reboot the whole controller
* Added Encryption support for API connection. KEY IS IN SECRETS.YAML Reprogram with your own generated key for proper security.
* Added substitutions for naming conventions for easier naming!

## [1.0.3]

* Added support for Hall Sensor Homing mechanism.

## [1.0.2]

### Added

* Added offline support. This will automatically open your Open AIR Valve when the connection to Home Assistant or your WI-FI network is lost

## [1.0.1]

### Changed

* Misnomer in the firmware for the fallback configuration hotspot that was using the old name instead of Open Air

## [1.0.0]

### Added

* Functionality to open and close the valve
* Look-up table to open/close valve based on effective amount of air flow instead of angle
* Boot valve position calibration using micro switch

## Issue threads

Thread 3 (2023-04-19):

A real life example

sanderlv, 2023-04-19:
Hi, thank you so much for creating this piece of hardware! It is now so handy to overcome the "issues" I had with the original print. the fact the fan would always auto turn on to 100% >65% hum was annoying and hard to change. I had "arne mauer" his print to arrange thing outside via HA but this did not always work as intended.
Now with this ESP board I can from within ESPhome create automations and turn on "auto" (or off :-)).

I have to change some internals on sensors to get a "fast" reaction on automations. By default in the SHT20 file this was set to 30000. I changed that to 5000 (5 seconds). then I created new sensors for HA with a throttle to 60s.

The result:
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

I may not be able to quickly react if questions are asked. Don;t be mad then 👍
disclaimer: This is my setup. Feel free to use or copy. But do no blame me for anything going wrong. It's your responsibility.

the change in SHT20:
```
  // the temperature 5s-30s. So lets poll at 4s, or half the response time.
  SHT20() : PollingComponent(5000) { }
  //was origineel 30000
```

the YAML:
```
esphome:
  name: esp32-duco-01
  platform: ESP32
  board: esp32dev
  libraries:
    - Wire
    - u-fire/uFire SHT20@^1.1.1
  includes:
    - custom_components/duco/sht20.h

substitutions:
  esp_name: esp32-duco-01

wifi:
  ssid: "IOT"
  password: !secret IOT_wifi_key
  use_address: 192.168.6.85
  domain: !secret domain
  # Enable fallback hotspot (captive portal) in case wifi connection fails
  ap:
    ssid: "${esp_name} Fallback Hotspot"
    password: !secret Fallback_Hotspot

captive_portal:

# Enable logging
logger:
  level: DEBUG

# Enable Home Assistant API
api:

ota:

web_server:
  port: 80

time:
  - platform: homeassistant
    id: homeassistant_time

#esp32_ble_tracker:
#bluetooth_proxy:

# ! Warning ! the original Duco sensor can only be connected on sensor connector 1!

#
uart:
#UART For Sensor 1
# - rx_pin: GPIO13
#   tx_pin: GPIO12
#   baud_rate: 9600
#   id: uart_sensor_1
#UART For Sensor 2
 - rx_pin: GPIO25
   tx_pin: GPIO26
   baud_rate: 9600
   id: uart_sensor_2

i2c:
#I2C For Sensor 1
- id: i2c_sensor_1
  sda: GPIO19
  scl: GPIO18
  scan: false
  frequency: 400kHz
#I2C For Sensor 2
- id: i2c_sensor_2
  sda: GPIO16
  scl: GPIO4
  scan: false
  frequency: 400kHz

# Status led
status_led:
  pin:
    number: GPIO33

#PWM output for controlling the motor.
output:
  - platform: ledc
    pin: GPIO15
    inverted: true
    id: open_air_mini

fan:
  - platform: speed
    output: open_air_mini
    name: "${esp_name} - Fan"
    id: ducofan

sensor:
  - <<: !include includes/include-wifi-signal.yaml
  - <<: !include includes/include-uptime-config.yaml

  - platform: pulse_counter
    pin: GPIO14
    unit_of_measurement: 'RPM'
    name: '${esp_name} - RPM'

  # SENSOR CONNECTOR 1 - original Duco sensor connected on sensor connector 1!
  - platform: custom
    lambda: |-
      auto sht20 = new SHT20();
      App.register_component(sht20);
      return {sht20->temperature_sensor, sht20->humidity_sensor, sht20->vpd_sensor, sht20->dew_point_sensor};
    sensors:
      - name: T
        internal: True
        id: sensor_temperature
        accuracy_decimals: 2
      - name: H
        id: sensor_humidity
        accuracy_decimals: 2
        internal: True
        on_value_range:
          - below: 65
            then:
              - if:
                  condition:
                    switch.is_on: ducoauto
                  then:
                    - fan.turn_on:
                        id: ducofan
                        speed: 10
          - above: 65
            below: 70
            then:
              - if:
                  condition:
                    switch.is_on: ducoauto
                  then:
                    - fan.turn_on:
                        id: ducofan
                        speed: 20
          - above: 70
            below: 75
            then:
              - if:
                  condition:
                    switch.is_on: ducoauto
                  then:
                    - fan.turn_on:
                        id: ducofan
                        speed: 40
          - above: 75
            below: 80
            then:
              - if:
                  condition:
                    switch.is_on: ducoauto
                  then:
                    - fan.turn_on:
                        id: ducofan
                        speed: 60
          - above: 80
            below: 85
            then:
              - if:
                  condition:
                    switch.is_on: ducoauto
                  then:
                    - fan.turn_on:
                        id: ducofan
                        speed: 75
          - above: 85
            then:
              - if:
                  condition:
                    switch.is_on: ducoauto
                  then:
                    - fan.turn_on:
                        id: ducofan
                        speed: 100
      - name: VPD
        id: sensor_vpd
        accuracy_decimals: 2
        internal: True
      - name: DP
        id: sensor_dew_point
        accuracy_decimals: 2
        internal: True

  # SENSOR CONNECTOR 2 - Combination of Senseair S8 & SHT-31 in one Sensor
  - platform: sht3xd
    i2c_id: i2c_sensor_2
    temperature:
      name: "${esp_name} - Sensor 2 - Temperature"
    humidity:
      name: "${esp_name} - Sensor 2 - Humidity"
      icon: mdi:water-percent
    address: 0x44
    update_interval: 30s
  - platform: senseair
    uart_id: uart_sensor_2
      #add sensor UART bus here
    co2:
      name: "${esp_name} - Sensor 2 - CO2"
    update_interval: 30s

  - platform: template
    name: "${esp_name} - Fan Speed"
    lambda: return id(ducofan).speed;
    update_interval: 3s
    unit_of_measurement: "%"
    accuracy_decimals: 0
    icon: mdi:fan

  - platform: copy
    name: "${esp_name} - Sensor 1 - Temperature"
    unit_of_measurement: °C
    accuracy_decimals: 2
    source_id: sensor_temperature
    filters:
      - throttle: 60s
  - platform: copy
    name: "${esp_name} - Sensor 1 - Humidity"
    unit_of_measurement: "%"
    accuracy_decimals: 2
    icon: mdi:water-percent
    source_id: sensor_humidity
    filters:
      - throttle: 60s
  - platform: copy
    name: "${esp_name} - Sensor 1 - Vapour-pressure deficit"
    unit_of_measurement: "kPa"
    accuracy_decimals: 2
    icon: mdi:air-humidifier
    source_id: sensor_vpd
    filters:
      - throttle: 60s
  - platform: copy
    name: "${esp_name} - Sensor 1 - Dew point"
    unit_of_measurement: °C
    accuracy_decimals: 2
    icon: mdi:water-thermometer-outline
    source_id: sensor_dew_point
    filters:
      - throttle: 60s

text_sensor:
  - <<: !include includes/include-uptime-human.yaml
  - <<: !include includes/include-esphome-version.yaml
  - <<: !include includes/include-wifi-info.yaml

switch:
  - <<: !include includes/include-generic-restart-switch.yaml

  - platform: template
    name: "${esp_name} - Automatisch"
    id: ducoauto
    optimistic : True
    restore_state: yes
    restore_mode: RESTORE_DEFAULT_ON
    icon: mdi:fan-auto

#https://github.com/Flamingo-tech/Open-AIR/tree/main/Open%20Air%20Mini/Software
```

Flamingo-tech, 2025-02-21:
@sanderlv Thanks for your example ^^! I will close this issue, for examples of semi-actual integrations please check: [Click](https://github.com/Flamingo-tech/Open-AIR/tree/main/Open%20AIR%20Mini/Software)

Closed 2025-02-21.

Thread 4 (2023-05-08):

Support for bypass

decramy, 2023-05-08:
My ventilationbox with Heat-Exchange (Dutch: WTW) supports bypassing the heat exchange for hot days (so the heat from the house is not put back into the house).
Also there is a pre-heating option available for this device (I dont have that).

Can you add one or more relais (with according software options) for this? Maybe with configurable names?

Flamingo-tech, 2025-07-06:
Hey @decramy for now WTWs are not supported! All supported models are listed on the open AIR Mini page : https://github.com/Flamingo-tech/Open-AIR/tree/main/Open%20AIR%20Mini

decramy, 2025-07-06:
erm yes... Thats why I mentioned it ;-) Not a bug report, more a feature request...

Closed 2025-07-06.

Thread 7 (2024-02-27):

Improvement for Open Air Valve YAML

roderik-maker, 2024-02-27:
I think the YAML file for the open air valve could benefit from adding some more checks. I made some additions and added a load of comments to the file. Wasn't sure if I should post here, or on the open-air-valve page, opted for the open-air-valve page but here is a [link to the thread](https://github.com/thomasvnl/esphome-open-air-valve/issues/3#issue-2156998379).

peterfortuin, 2025-02-19:
@roderik-maker, it seems that your link is not working any more.

roderik-maker, 2025-07-07:
I'll try find some time tonight to share it again

roderik-maker, 2025-07-09:
Its been a very bussy week and I can't find the original either anymore. Here is my current config for 1 of my valves, I think is the best version I currently have. I'll try find time on Saturday to clean it up and add some comments and explanations.

```
substitutions:
  device_friendly_name: "Valve-1"
  valve_as_number_id: "valve_capacity"
  my_stepper_id: "my_stepper"
  valve_capacity_lookup_table: id(valve_capacity_lookup_table)

esphome:
  name: open-air-valve-1
  friendly_name: ${device_friendly_name}
  name_add_mac_suffix: False

  on_boot:
    - priority: 700
      then:
      - stepper.set_acceleration:
          id: my_stepper
          acceleration: inf
      - stepper.set_deceleration:
          id: my_stepper
          deceleration: inf
      - stepper.report_position:
          id: my_stepper
          position: 0
      - stepper.set_target:
          id: my_stepper
          target: !lambda 'return id(valve_capacity_lookup_table)[10];'
      - wait_until:
          condition:
            lambda:
              return id(my_stepper).current_position == id(my_stepper).target_position;
      - stepper.set_speed:
          id: my_stepper
          speed: 150 steps/s
      - if:
          condition:
            binary_sensor.is_off: valve_homing_switch
          then:
          - while:
              condition:
                binary_sensor.is_off: valve_homing_switch
              then:
                - stepper.report_position:
                    id: my_stepper
                    position: 0
                - stepper.set_target:
                    id: my_stepper
                    target: -1
                - wait_until:
                    condition:
                      lambda:
                        return id(my_stepper).current_position <= id(my_stepper).target_position;
      - stepper.report_position:
          id: my_stepper
          position: 0
      - stepper.set_target:
          id: my_stepper
          target: 0
      - stepper.set_speed:
          id: my_stepper
          speed: 350 steps/s

esp32:
  board: esp32dev
  framework:
    type: esp-idf

# Enable logging
logger:
  level: DEBUG

# This is optional and can be commented out to disable the Web Server
web_server:
  port: 80

# Enable Home Assistant API
api:
  encryption:
    key: "xxxxxxxxxxxxxxx"

ota:
  password: "xxxxxxxxxxxxxxxxx"
  platform: esphome

wifi:
  ssid: !secret wifi_ssid
  password: !secret wifi_password
  use_address: "192.168.178.88"

  # Enable fallback hotspot (captive portal) in case wifi connection fails
  ap:
    ssid: "Open-Air-${device_friendly_name}"
    password: "xxxxxxxxxxxxx"

captive_portal:

globals:
  - id: valve_capacity_lookup_table
    type: std::vector<int>
    restore_value: no
    initial_value: '{0,47,66,82,94,106,116,125,134,142,150,158,165,172,178,185,191,197,203,209,215,220,225,231,236,241,246,251,256,261,265,270,275,279,284,288,292,297,301,305,309,314,318,322,326,330,334,338,342,346,350,353,357,361,365,368,372,376,380,383,387,391,394,398,401,405,409,412,416,419,423,426,430,433,437,440,443,447,450,454,457,461,464,467,471,474,478,481,484,488,491,494,498,501,504,508,511,514,518,521,525}'

number:
  - platform: template
    name: "Valve Capacity %"
    id: valve_capacity
    optimistic: true
    restore_value: no
    initial_value: 0
    min_value: 0
    max_value: 100
    step: 10
    mode: slider
    on_value:
      then:
        - stepper.set_target:
            id: my_stepper
            target: !lambda |-
              if (x <= 0) {
                return 0;
              } else if(x >= 100) {
                return 525;
              } else if (x > 0 && x < 100) {
                int steps = id(valve_capacity_lookup_table)[x];
                return steps;
              } else {
                return 0;
              }

status_led:
  pin:
    number: GPIO33

uart:
#UART For Sensor 1
-  id: uart_sensor_1
   rx_pin: GPIO25
   tx_pin: GPIO26
   baud_rate: 9600

i2c:
#I2C For Sensor 1
- id: i2c_sensor_1
  sda: GPIO16
  scl: GPIO4
  scan: false
  frequency: 400kHz

cover:
  - platform: template
    name: "Valve"
    id: valve
    lambda: |-
      if (id(my_stepper).current_position <= 0) {
        return COVER_CLOSED;
      } else if (id(my_stepper).current_position > 0 && id(my_stepper).current_position <= 100) {
        return COVER_OPEN;
      } else {
        return {};
      }
    open_action:
      - number.set:
          id: valve_capacity
          value: 100
      - stepper.set_target:
          id: my_stepper
          target: 525
    close_action:
      - number.set:
          id: valve_capacity
          value: 0
      - stepper.set_target:
          id: my_stepper
          target: 0

stepper:
  - platform: uln2003
    id: my_stepper
    # pin_a: GPIO12
    # pin_b: GPIO13
    # pin_c: GPIO14
    # pin_d: GPIO15
    pin_a: GPIO15  # Swap pin_a and pin_d
    pin_b: GPIO14  # Swap pin_b and pin_c
    pin_c: GPIO13
    pin_d: GPIO12
    max_speed: 350 steps/s
    acceleration: inf
    deceleration: inf
    sleep_when_done: true

switch:
  - platform: restart
    name: "Reboot valve controller to recalibrate"

binary_sensor:
  - platform: gpio
    id: valve_homing_switch
    pin: GPIO35
    name: "Valve Closed Switch"
    on_press:
      then:
      - delay: 0.7s
      - if:
          condition:
            - lambda: |-
                return (id(valve).position == COVER_CLOSED);
            - binary_sensor.is_off: valve_homing_switch
          then:
            - script.execute: recalibrate_valve_to_zero

sensor:
  - platform: scd4x
    co2:
      name: "${device_friendly_name} Co2 Sensor"
    temperature:
      name: "${device_friendly_name} Temperature Sensor"
    humidity:
      name: "${device_friendly_name} Humidity Sensor"

script:
  - id: recalibrate_valve_to_zero
    then:
      - stepper.report_position:
          id: my_stepper
          position: 0
      - stepper.set_target:
          id: my_stepper
          target: !lambda 'return id(valve_capacity_lookup_table)[30];'
      - wait_until:
          condition:
            lambda:
              return id(my_stepper).current_position == id(my_stepper).target_position;
      - if:
          condition:
            binary_sensor.is_off: valve_homing_switch
          then:
          - while:
              condition:
                binary_sensor.is_off: valve_homing_switch
              then:
                - stepper.report_position:
                    id: my_stepper
                    position: 0
                - stepper.set_target:
                    id: my_stepper
                    target: -1
                - wait_until:
                    condition:
                      lambda:
                        return id(my_stepper).current_position <= id(my_stepper).target_position;

```
The problem is, if it is really stuck, it'll stay stuck. I still need to add a loop counter that throws an error after x-step attempts and then blocks the stepper motor from moving to prevent damage.

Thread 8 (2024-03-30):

Can ping but not discovered by HA, no webserver

wpeterw, 2024-03-30:
Just installed my Openair Mini. It connects to my wifi and I can ping the ip address but it's not discovered by HA and no webserver on port 80, any ideas ?

`❯ sudo nmap -sT 192.168.1.202
Starting Nmap 7.80 ( https://nmap.org ) at 2024-03-30 12:51 CET
Nmap scan report for 192.168.1.202
Host is up (0.011s latency).
All 1000 scanned ports on 192.168.1.202 are closed`

thomasvnl, 2024-03-30:
Did you use your own custom ESPHome config? If so, can you post it here (without any secrets)?

wpeterw, 2024-03-31:
RH sensor was connected to the wrong header, so the device was in a bootloop.

Closed 2024-03-31.

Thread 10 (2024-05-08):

Question Ducobox silent humidity sensor

remcoongit, 2024-05-08:
Hi,

I just got the hardware and installed it in homeassistant, esphome. Now I cannot find how to configure my existing sensor on the esphome yaml.

It's the humidty sensor that came with the duco box silent, I assume uart as writen in the readme's here. But I cannot figure out what to use as sensor in the yaml to make it show up with valid data in homeassistant.

Thanks,

remcoongit, 2024-05-11:
Issue resolved with standard yaml. Was some problem with uploading the firmware.

Closed 2024-05-11.

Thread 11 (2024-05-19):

Use ESPHome/Home Assitant valve component/entity

markbergsma, 2024-05-19:
I updated my Open AIR Valve ESPHome code to use the newer valve component to control using a single entity, as opposed to the old two entities. I replaced the old "number" and "cover" blocks by:

```
valve:
  - platform: template
    name: "Valve"
    id: airvalve
    icon: mdi:valve
    has_position: true
    optimistic: true
    lambda: |-
      if (id(my_stepper).target_position == 0) {
        return VALVE_CLOSED;
      }
      else {
        return id(airvalve).position;
      }
    open_action:
      - stepper.set_target:
          id: my_stepper
          target: 525
    close_action:
      - stepper.set_target:
          id: my_stepper
          target: 0
    position_action:
      then:
        - stepper.set_target:
            id: my_stepper
            target: !lambda |-
              if (pos <= 0.0) {
                return 0;
              } else if(pos >= 1.0) {
                return 525;
              } else if (pos > 0.0 && pos < 1.0) {
                int steps = id(valve_capacity_lookup_table)[pos * 100];
                return steps;
              } else {
                return 0;
              }
```

Flamingo-tech, 2025-07-06:
Great suggestion! We will change the valve code to support this! I will keep this ticket open until we have changed the code :D!

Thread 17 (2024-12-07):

air_humidity is not defined

jahierwan, 2024-12-07:
I've tryied to use `disconnected-mode-with-humidity.yaml` instead of `disconnected-mode-without-humidity.yaml`
by switching the comment mark in `open-air-mini.yaml`::160, and then esphome fails to compile `open-air-mini.yaml`
because `air_humidity` is not defined and indeed it isn't.

https://github.com/Flamingo-tech/Open-AIR/blob/06d94d354e306479dbb5e57fdb917247b8f7ebf8/Open%20AIR%20Mini/Software/disconnected-mode-with-humidity.yaml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

And Tx for providing that great piece of engineering BTW!

jahierwan, 2024-12-07:
ah, ok, I found the problem. I should have RTFM, sorry

Closed 2024-12-07.

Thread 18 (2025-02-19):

ESPhome update 2025.2 gives an error

sanderlv, 2025-02-19:
```
INFO ESPHome 2025.2.0
INFO Reading configuration /config/esphome/esp32-duco-01.yaml...
INFO Detected timezone 'Europe/Amsterdam'
WARNING GPIO15 is a strapping PIN and should only be used for I/O with care.
Attaching external pullup/down resistors to strapping pins can cause unexpected failures.
See https://esphome.io/guides/faq.html#why-am-i-getting-a-warning-about-strapping-pins
Failed config

sensor.custom: [source /config/esphome/esp32-duco-01.yaml:106]

  The "custom" component has been removed. Consider conversion to an external component.
  https://esphome.io/guides/contributing#a-note-about-custom-components.
  platform: custom
  lambda: |-
    auto sht20 = new SHT20();
    App.register_component(sht20);
    return {sht20->temperature_sensor, sht20->humidity_sensor, sht20->vpd_sensor, sht20->dew_point_sensor};
  sensors:
    - name: T
      internal: True
      id: sensor_temperature
      accuracy_decimals: 2
    - name: H
```
Is this something "easy" to change?

https://esphome.io/guides/contributing#a-note-about-custom-components

thomasvnl, 2025-02-19:
Hi Sander,

The easiest for now would be to remain on a lower version of ESPHome for
this device. I do not have a better answer at this time.

Op wo 19 feb 2025 om 13:46 schreef Sender ***@***.***>:

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

peterfortuin, 2025-02-19:
I'm wondering what kind of config yaml you have, because the current yaml's in the repo don't have custom components.

thomasvnl, 2025-02-21:
@sanderlv I see you've reacted with an unhappy frowning smiley, but my suggestion to lower the version of ESPHome (for this specific device) would be the "Is this something "easy" to change?" solution (for now).

Flamingo-tech, 2025-02-21:
Please use this integration method for the SHT-20 Sensor: [Click](https://github.com/Flamingo-tech/Open-AIR/tree/main/Open%20AIR%20Mini/Software#sensor-support-SHT-20)

Example:

`external_components:
  - source: github://dmaasland/esphome@sht2x
    components: [ sht2x ]`

`
  - platform: sht2x
    i2c_id: i2c_sensor_1
    temperature:
      name: "Open AIR Mini x Temperature"
      id: air_temperature
      accuracy_decimals: 2
    humidity:
      name: "Open AIR Mini x Humidity"
      id: air_humidity
      accuracy_decimals: 2
    update_interval: 30s
`

This should solve your issue. The method you are trying to use was the old method. If you need help with your new YAML please mail : flamingo-tech@protonmail.com

sanderlv, 2025-03-01:
Have a look here: this solves the issue temporarily:

https://github.com/robertklep/esphome-custom-component

Closed 2025-02-21.

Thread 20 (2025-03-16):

Usable in Denmark?

KlavsKlavsen, 2025-03-16:
I'm looking for a solution for a co2 buildup problem where our ventilation system simply isn't enough.
ventilation systems is mandatory in Denmark since 2008 in all houses - and they all use this same system:
https://www.lavprisvvs.dk/air2trust-udsugningsventil-kl-med-ramme-oe100-mm-639458 inlet valves mounted on a 90degree round bend (100mm or in a few cases 125mm metal tube).

I have 8 inlet valves - one for each room that isn't an "outlet room" - and the co2 buildup follows the family. So during the day - the problem is in the office room.. during dinner - its in the kitchen.. and at night - its a problem in the bedroom.

My thinking was that if I could replace my inlet valves with some digitally controller air inlet valve - and mount some zigbee co2 sensors - I could set this up to automaticly follow co2 pressure.

I would be very happy to buy all 8 from your tindie shop - so I don't have to solder - if they can work for this danish system? (I tried to write via tindie first - but it fails sending)

KlavsKlavsen, 2025-03-23:
I was thinking a version could be made with a round ring (of just below 100mm or 125mm) - to fit inside the ventilation tube - just before the outlet valve - a "fat ring - with all same components as yours has on the outside now" - and an adjusted "valve" - in the middle. That would make it work with existing ventilation.. WDYT ?
Just an idea atleast :)

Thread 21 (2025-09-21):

How do you power the OpenAIR valve?

DeWildeDaan, 2025-09-21:
This project seems absolutely awesome and I’m reading trough the docs because I may want to install this on my Orcon MVS-15RHB.
But I’m struggling to find how to power the valves?
It is possible I’m overlooking something but is there support to plug them into the OpenAIR mini board or is there some kind of breakout/distribution board where you can plug in the mains and it is distributes to the OpenAIR mini and x amount of valves?
Anyway, I’m curious how you guys did it, keep up the awesome work on the project! 😄

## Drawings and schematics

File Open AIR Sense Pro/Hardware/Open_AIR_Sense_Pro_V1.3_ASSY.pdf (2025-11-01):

## Fabrication Specifications

# Fabrication Information

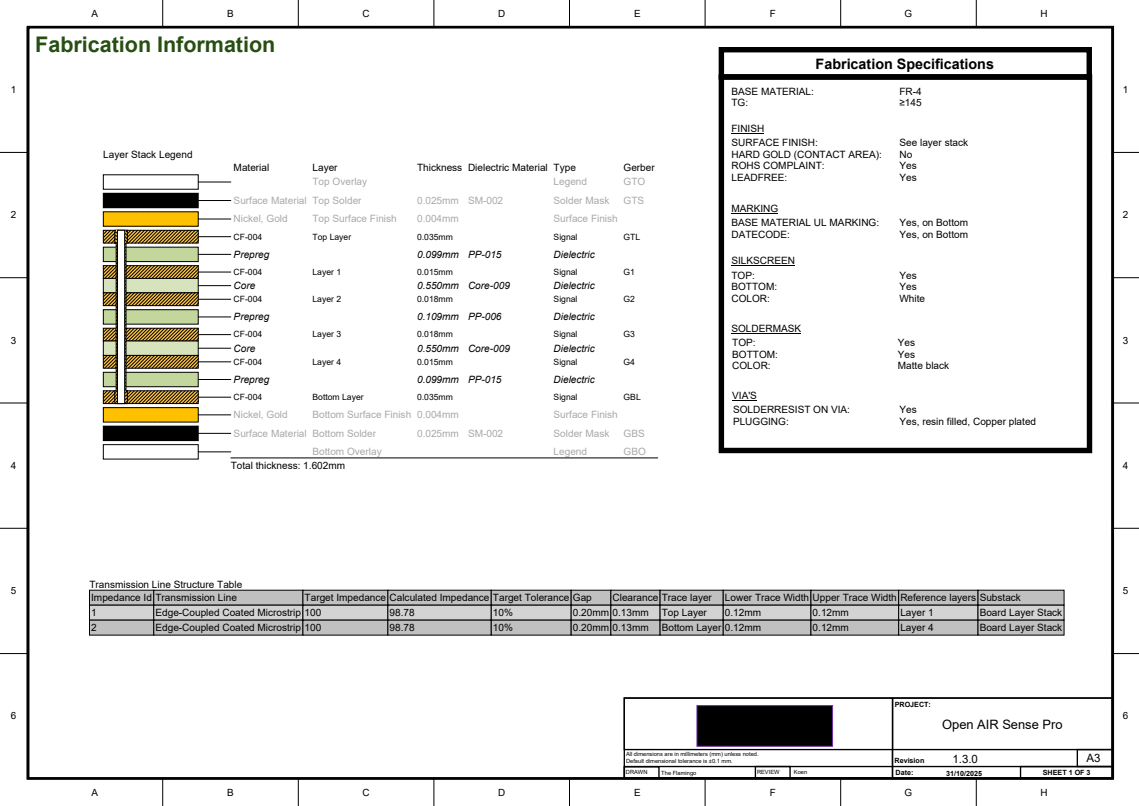
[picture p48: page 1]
Material; Layer; Thickness Dielectric Material Type; Gerber; Top Overlay; Legend; GTO; Surface Material Top Solder; Solder Mask; GTS; Nickel, Gold; Top Surface Finish; Surface Finish; Top Layer; Signal; GTL; Prepreg; Dielectric; Layer 1; Core; 0.550mm Core-009; Layer 2; Layer 3; Layer 4; Bottom Layer; GBL; Bottom Surface Finish 0.004mm; Surface Material Bottom Solder; GBS; Bottom Overlay; GBO; Total thickness: 1.602mm; Yes Yes Matte black; Yes Yes White; TOP: BOTTOM: COLOR:; SOLDERMASK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

FINISH
SURFACE FINISH:
HARD GOLD (CONTACT AREA):
ROHS COMPLAINT:
LEADFREE:

See layer stack
Yes

Layer Stack Legend

MARKING
BASE MATERIAL UL MARKING:
DATECODE:

Yes, on Bottom

VIA'S
SOLDERRESIST ON VIA:
PLUGGING:

Yes, resin filled, Copper plated

Transmission Line Structure Table
Impedance Id

Transmission Line
Edge-Coupled Coated Microstrip

Substack
Board Layer Stack

Open AIR Sense Pro

All dimensions are in millimeters (mm) unless noted.
Default dimensional tolerance is ±0.1 mm.
DRAWN

# Component Placement - Top & Bottom

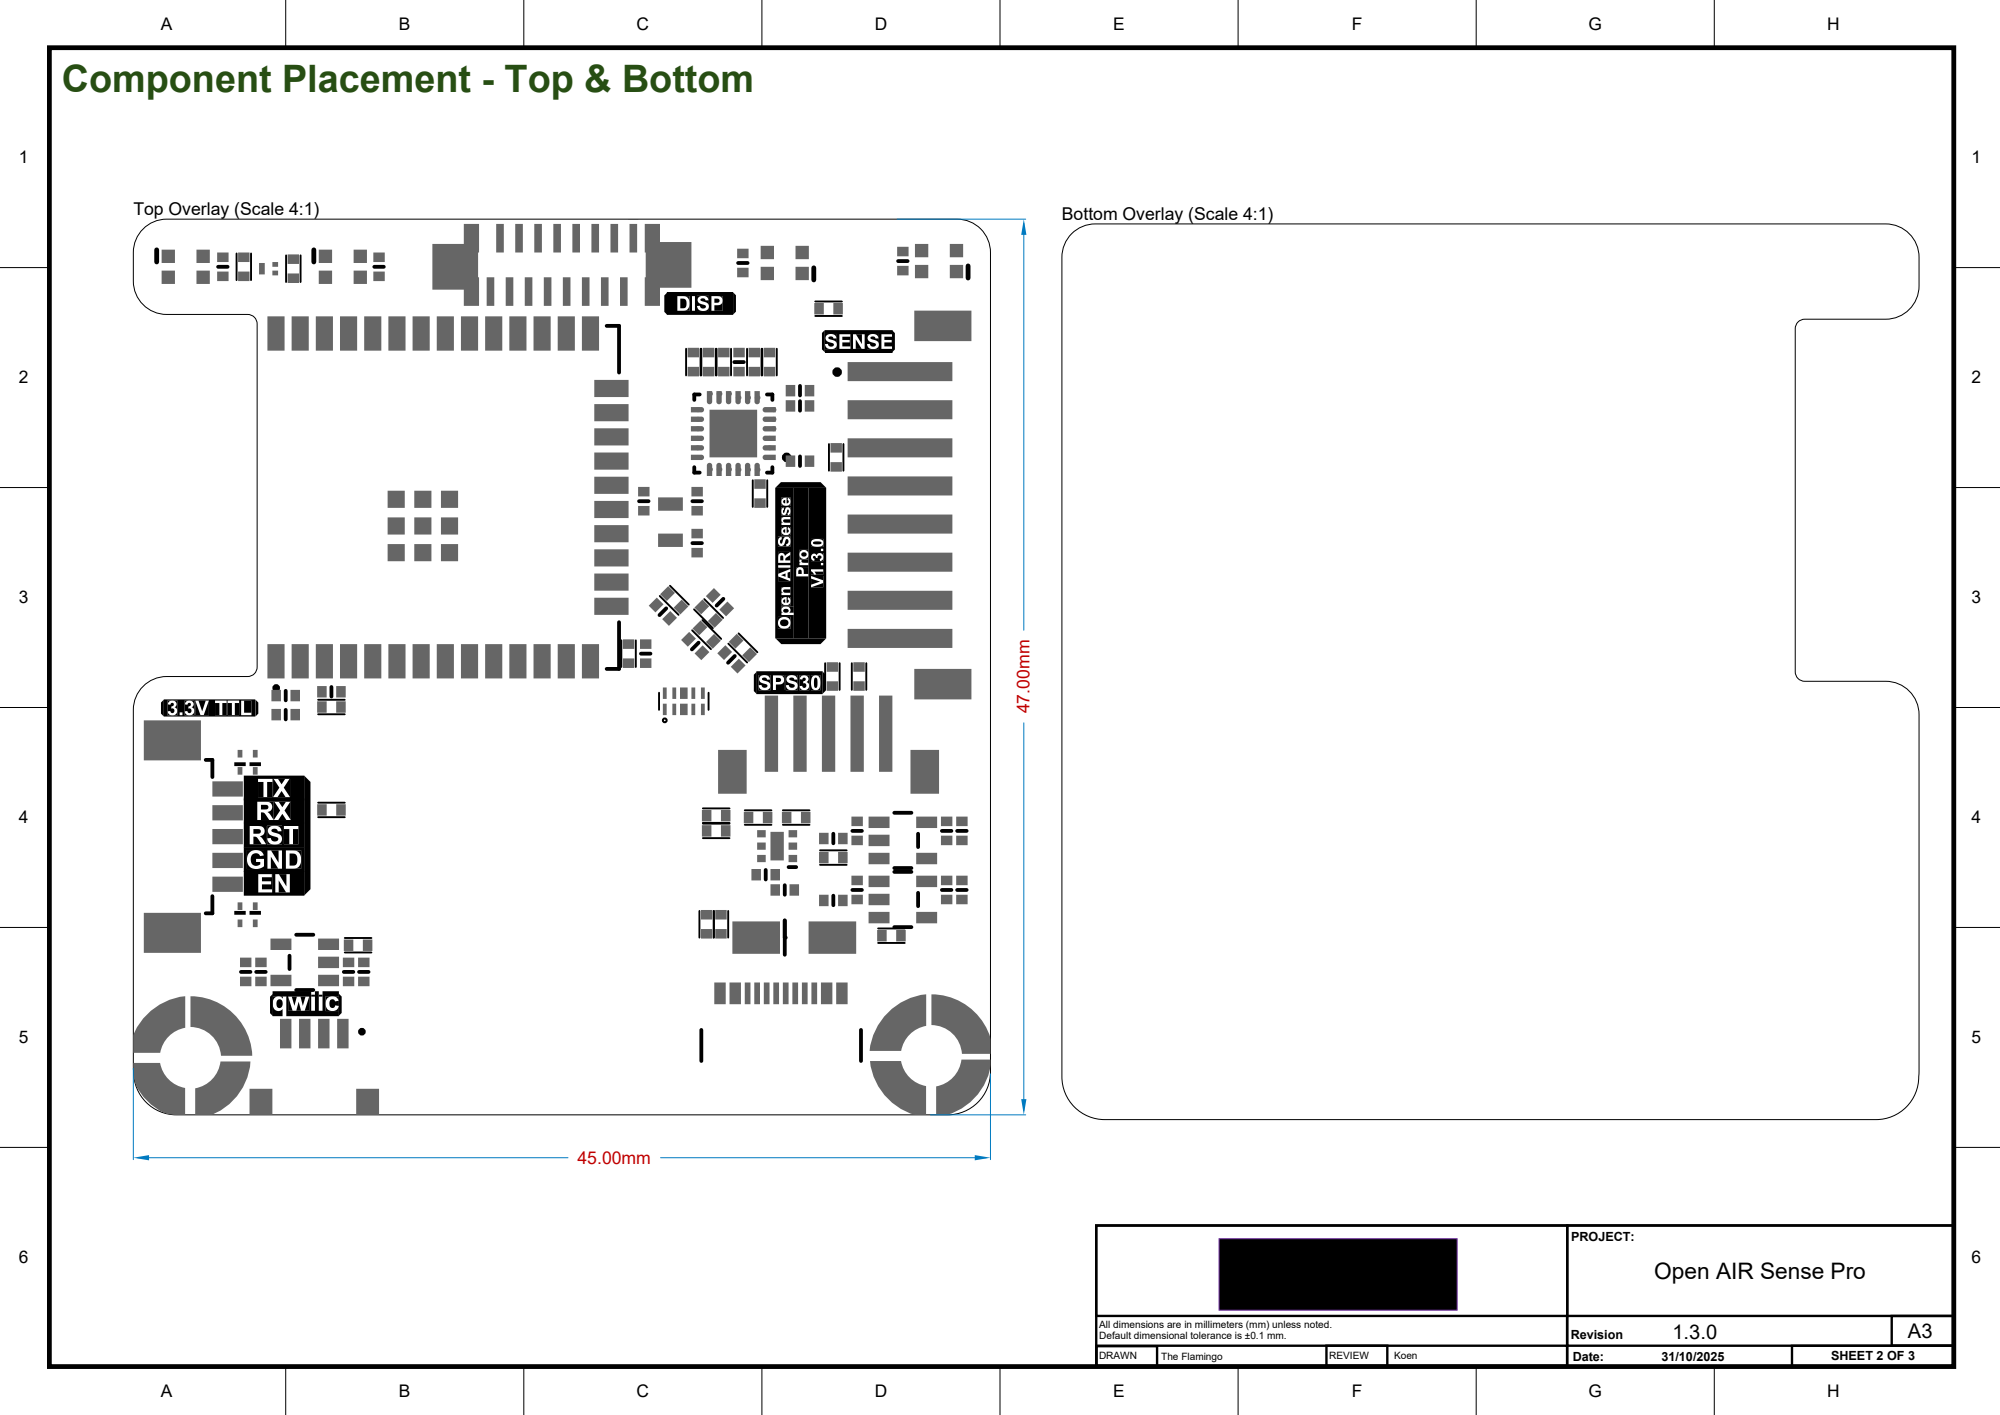
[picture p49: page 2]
Top Overlay (Scale 4:1); Bottom Overlay (Scale 4:1); PROJECT:

Open AIR Sense Pro

# Realistic view - TOP & BOT

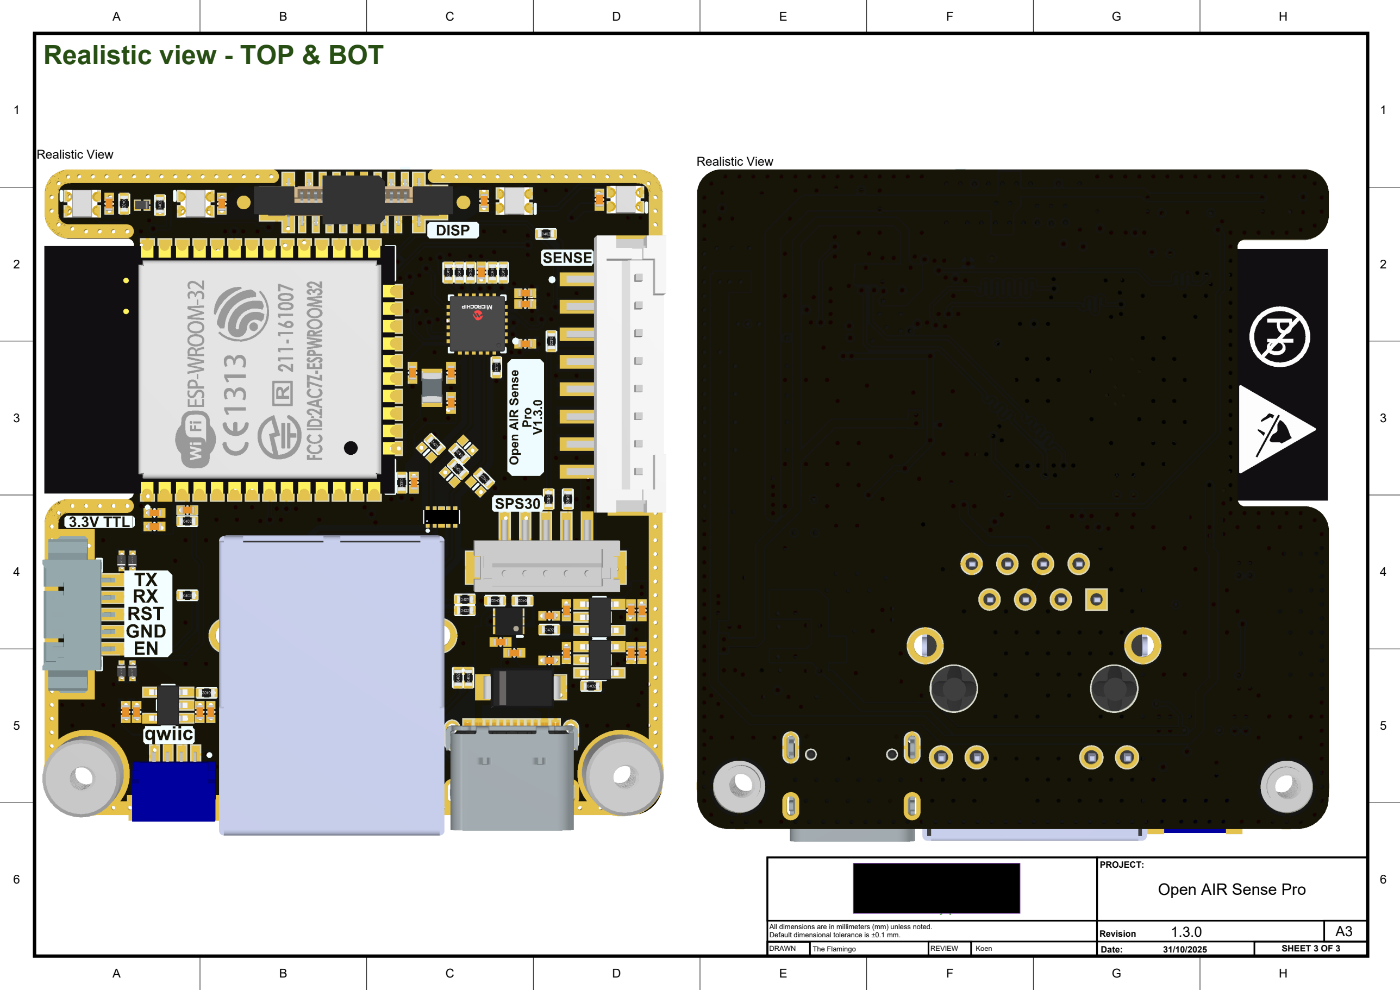
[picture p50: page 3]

1 | 1
2 | 2
3 | 3
4 | 4
5 | 5
6 | 6

Realistic View

PROJECT:

## Open AIR Sense Pro

Realistic View

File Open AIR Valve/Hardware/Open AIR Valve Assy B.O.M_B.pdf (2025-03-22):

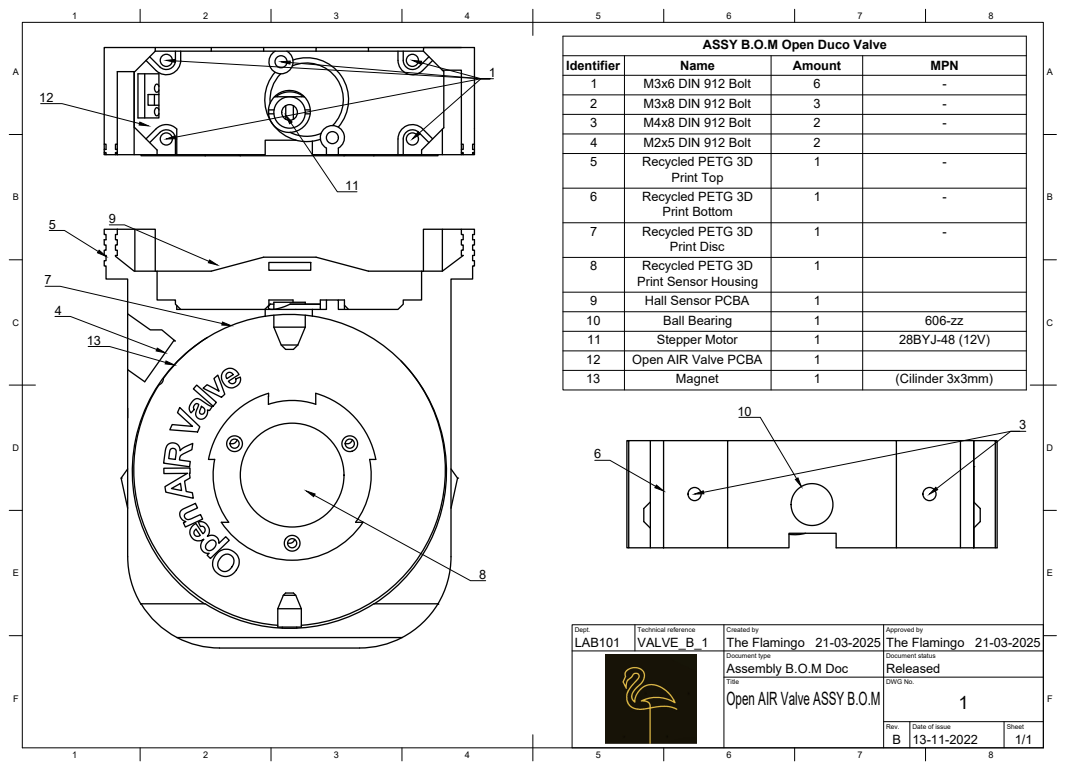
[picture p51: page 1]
Title; DWG No.; Rev.; Date of issue; Sheet; Open AIR Valve ASSY B.O.M; M3x6 DIN 912 Bolt; M3x8 DIN 912 Bolt; M4x8 DIN 912 Bolt; M2x5 DIN 912 Bolt

ASSY B.O.M Open Duco Valve

5 | Recycled PETG 3D Recycled PETG 3D Print Top | 1 | - 6

Recycled PETG 3D Print Bottom | 1 | - 7

Recycled PETG 3D Print Disc | 1 | - 8

Print Sensor Housing | 1

9 | Hall Sensor PCBA | 1
10 | Ball Bearing | 1 | 606-zz
11 | Stepper Motor | 1 | 28BYJ-48 (12V)
12 | Open AIR Valve PCBA | 1
13 | Magnet | 1 | (Cilinder 3x3mm)

Dept. LAB101 | Technical reference VALVE_B_1 | Created by The Flamingo 21-03-2025 | Approved by The Flamingo 21-03-2025

Document type Assembly B.O.M Doc | Document status Released

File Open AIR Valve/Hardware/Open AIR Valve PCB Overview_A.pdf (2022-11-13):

# Open Air Valve Overview

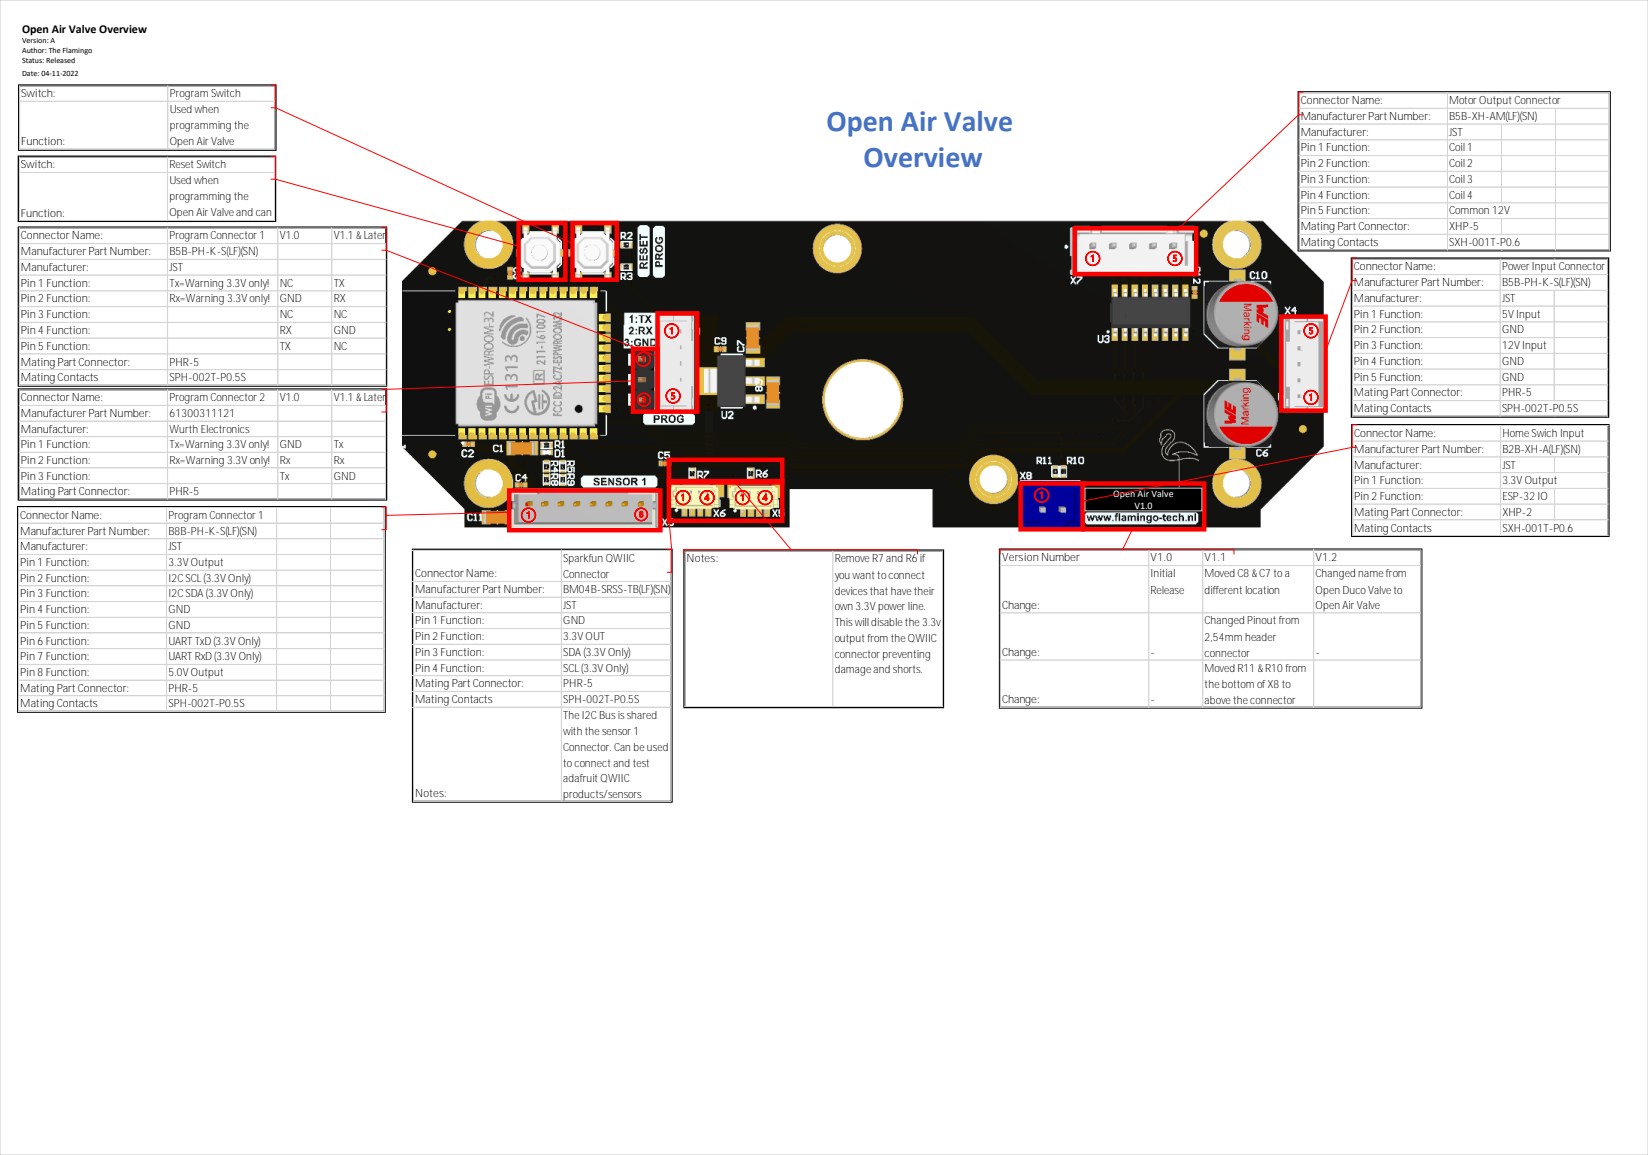
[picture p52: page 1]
Connector Name:; Power Input Connector; Manufacturer Part Number:; Manufacturer:; JST; Pin 1 Function:; 5V Input; Pin 2 Function:; GND; Pin 3 Function:; 12V Input; Pin 4 Function:; Pin 5 Function:; Coil 2; Coil 3; Version Number; Change:; connector; Switch:; Reset Switch; Function:; Tx=Warning 3.3V only!; Rx=Warning 3.3V only!; Mating Part Connector:; PHR-5; Mating Contacts; SPH-002T-P0.5S; Sparkfun QWIIC Connector; SCL (3.3V Only); Notes:; Remove R7 and R6 if

Open Air Valve Overview
Version: A
Author: The Flamingo
Status: Released
Date: 04-11-2022

Switch: | Program Switch
Function: | Used when programming the Open Air Valve

Connector Name: | Motor Output Connector
Manufacturer Part Number: | B5B-XH-AM(LF)(SN)
Manufacturer: | JST
Pin 1 Function: | Coil 1

Used when
programming the
Open Air Valve and can

Pin 4 Function: | Coil 4
Pin 5 Function: | Common 12V
Mating Part Connector: | XHP-5
Mating Contacts | SXH-001T-P0.6

Connector Name: | Program Connector 1 | V1.0 | V1.1 & Later
Manufacturer Part Number: | B5B-PH-K-S(LF)(SN)

Mating Part Connector: | PHR-5
Mating Contacts | SPH-002T-P0.5S

Connector Name: | Program Connector 2 | V1.0 | V1.1 & Later
Manufacturer Part Number: | 61300311121
Manufacturer: | Wurth Electronics
Pin 1 Function: | Tx=Warning 3.3V only! | GND | Tx
Pin 2 Function: | Rx=Warning 3.3V only! | Rx | Rx
Pin 3 Function: | | Tx | GND

Connector Name: | Home Swich Input
Manufacturer Part Number: | B2B-XH-A(LF)(SN)
Pin 1 Function: | 3.3V Output
Pin 2 Function: | ESP-32 IO
Mating Part Connector: | XHP-2

Open Air Valve

Connector Name: | Program Connector 1
Manufacturer Part Number: | B8B-PH-K-S(LF)(SN)
Pin 2 Function: | I2C SCL (3.3V Only)
Pin 3 Function: | I2C SDA (3.3V Only)
Pin 4 Function: | GND
Pin 5 Function: | GND
Pin 6 Function: | UART TxD (3.3V Only)
Pin 7 Function: | UART RxD (3.3V Only)
Pin 8 Function: | 5.0V Output

you want to connect
devices that have their
own 3.3V power line.
This will disable the 3.3v
output from the QWIIC
connector preventing
damage and shorts.

Change: | Initial Release | Moved C8 & C7 to a different location | Changed name from Open Duco Valve to Open Air Valve

Manufacturer Part Number: | BM04B-SRSS-TB(LF)(SN)

Changed Pinout from
2,54mm header
Moved R11 & R10 from
the bottom of X8 to
above the connector

Pin 2 Function: | 3.3V OUT
Pin 3 Function: | SDA (3.3V Only)

Notes: | The I2C Bus is shared with the sensor 1 Connector. Can be used to connect and test adafruit QWIIC products/sensors

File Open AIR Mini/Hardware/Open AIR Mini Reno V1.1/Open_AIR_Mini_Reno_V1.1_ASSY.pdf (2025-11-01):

## Fabrication Specifications

# Fabrication information

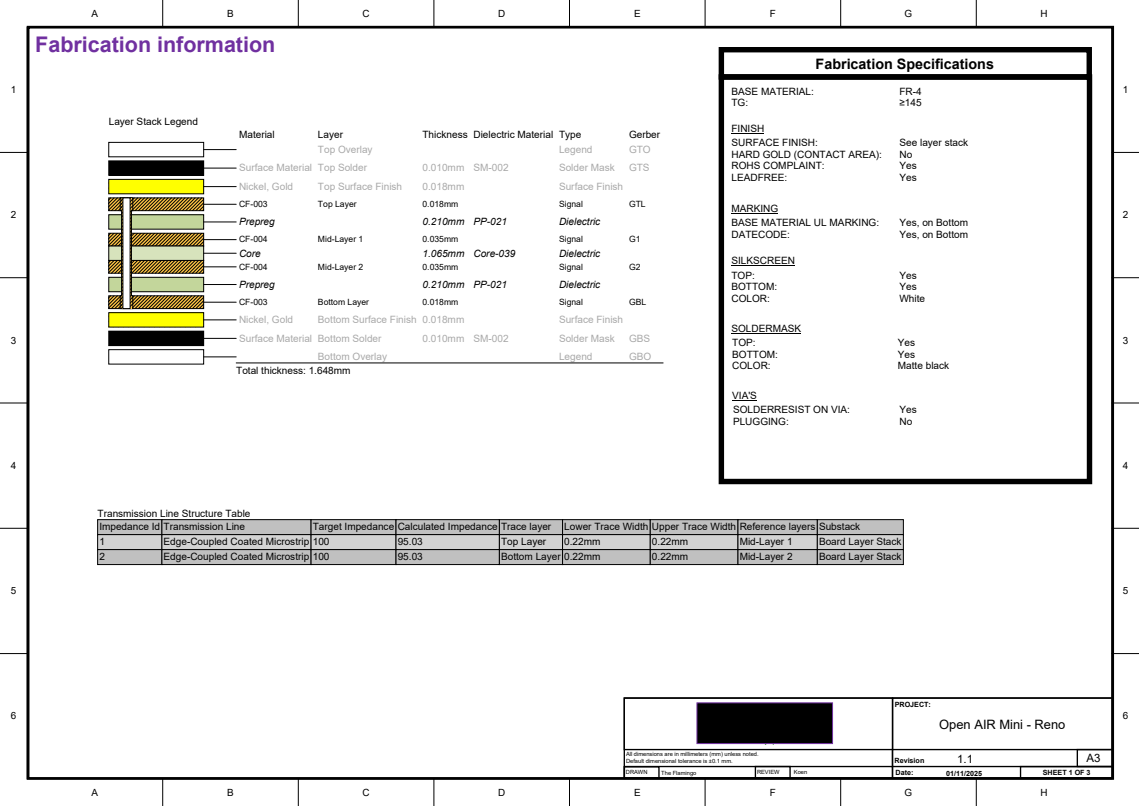
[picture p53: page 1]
Material; Layer; Thickness Dielectric Material Type; Gerber; Top Overlay; Legend; GTO; Surface Material Top Solder; Solder Mask; GTS; Nickel, Gold; Top Surface Finish; Surface Finish; Top Layer; Signal; GTL; Prepreg; Dielectric; Mid-Layer 1; Core; 1.065mm Core-039; Mid-Layer 2; Bottom Layer; GBL; Bottom Surface Finish 0.018mm; Surface Material Bottom Solder; GBS; Bottom Overlay; GBO; Total thickness: 1.648mm; Yes No; Yes Yes Matte black; Yes Yes White; TOP: BOTTOM: COLOR:; SOLDERMASK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

Layer Stack Legend

FINISH
SURFACE FINISH:
HARD GOLD (CONTACT AREA):
ROHS COMPLAINT:
LEADFREE:

See layer stack
Yes

MARKING
BASE MATERIAL UL MARKING:
DATECODE:

Yes, on Bottom

VIA'S
SOLDERRESIST ON VIA:
PLUGGING:

Transmission Line Structure Table
Impedance Id

Transmission Line
Edge-Coupled Coated Microstrip

Substack
Board Layer Stack

Open AIR Mini - Reno

All dimensions are in millimeters (mm) unless noted.
Default dimensional tolerance is ±0.1 mm.
DRAWN

# Component placement - TOP &

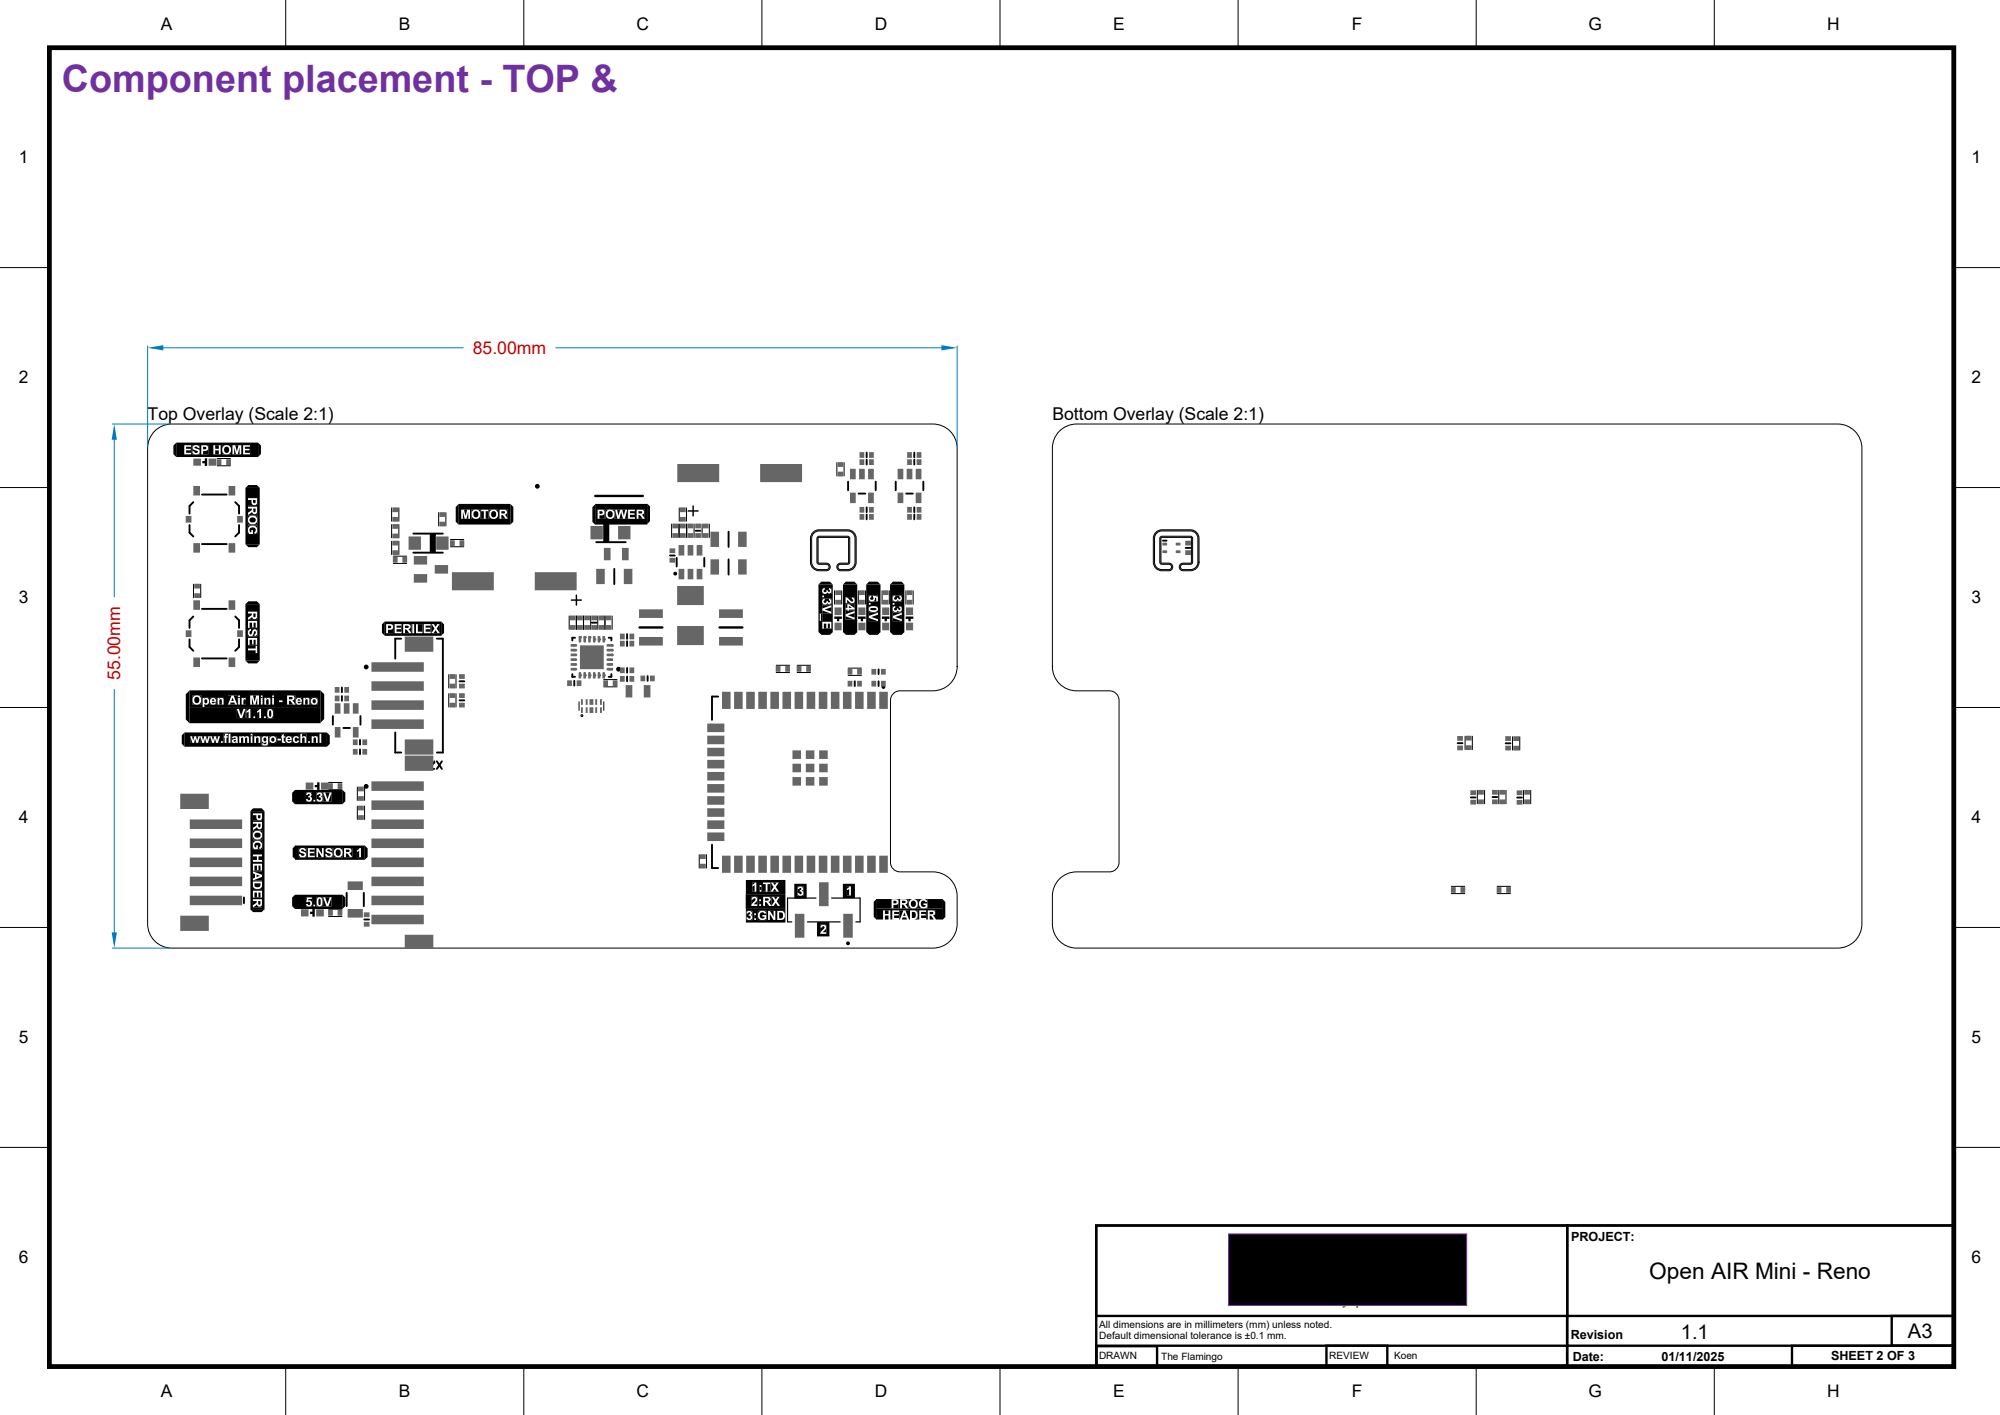
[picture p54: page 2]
Top Overlay (Scale 2:1); Bottom Overlay (Scale 2:1); PROJECT:

Open AIR Mini - Reno

# Realistic view - TOP & BOT Realistic View

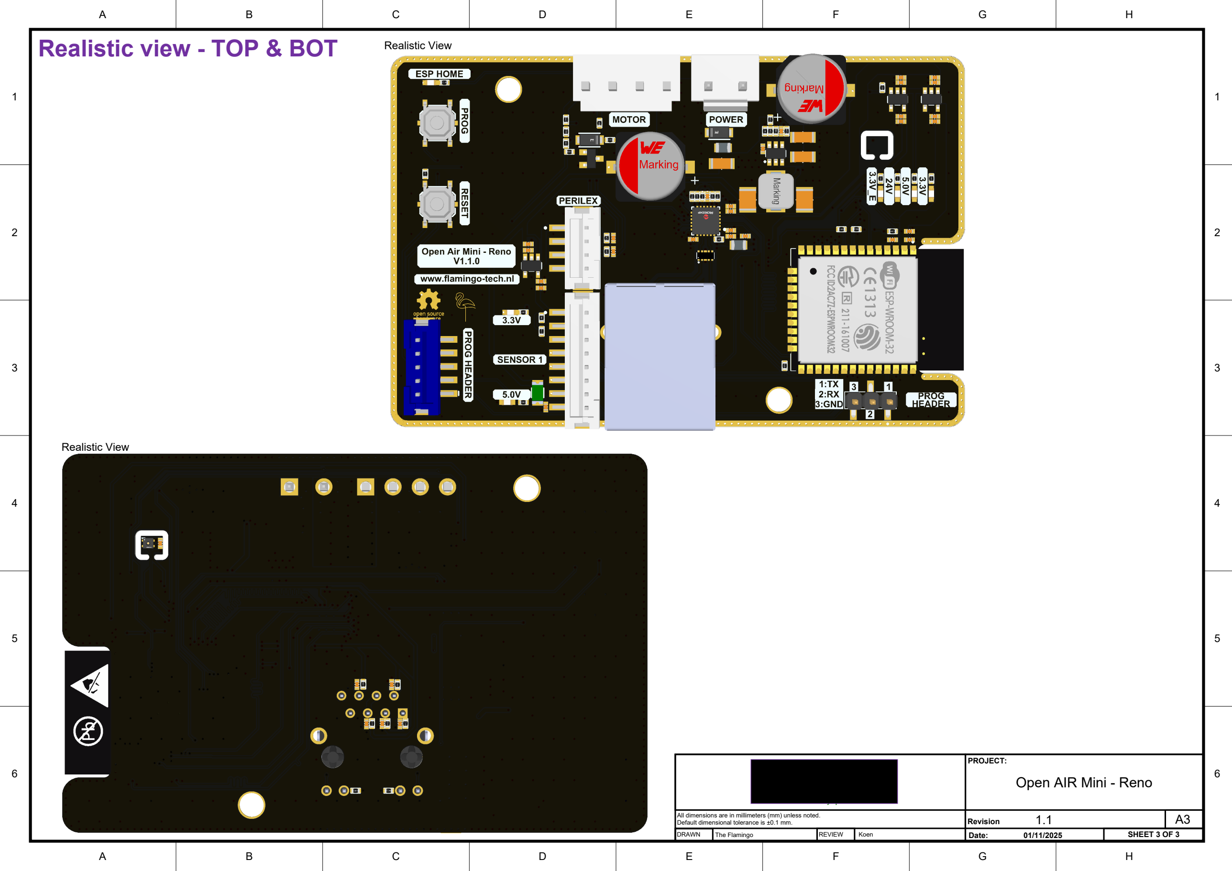
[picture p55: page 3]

1 | 1
2 | 2
3 | 3
4 | 4
5 | 5
6 | 6

Realistic View

PROJECT:

## Open AIR Mini - Reno

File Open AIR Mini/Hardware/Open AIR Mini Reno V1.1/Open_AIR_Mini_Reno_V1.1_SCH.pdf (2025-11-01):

# WIFI/BLE

# RH-Sensor

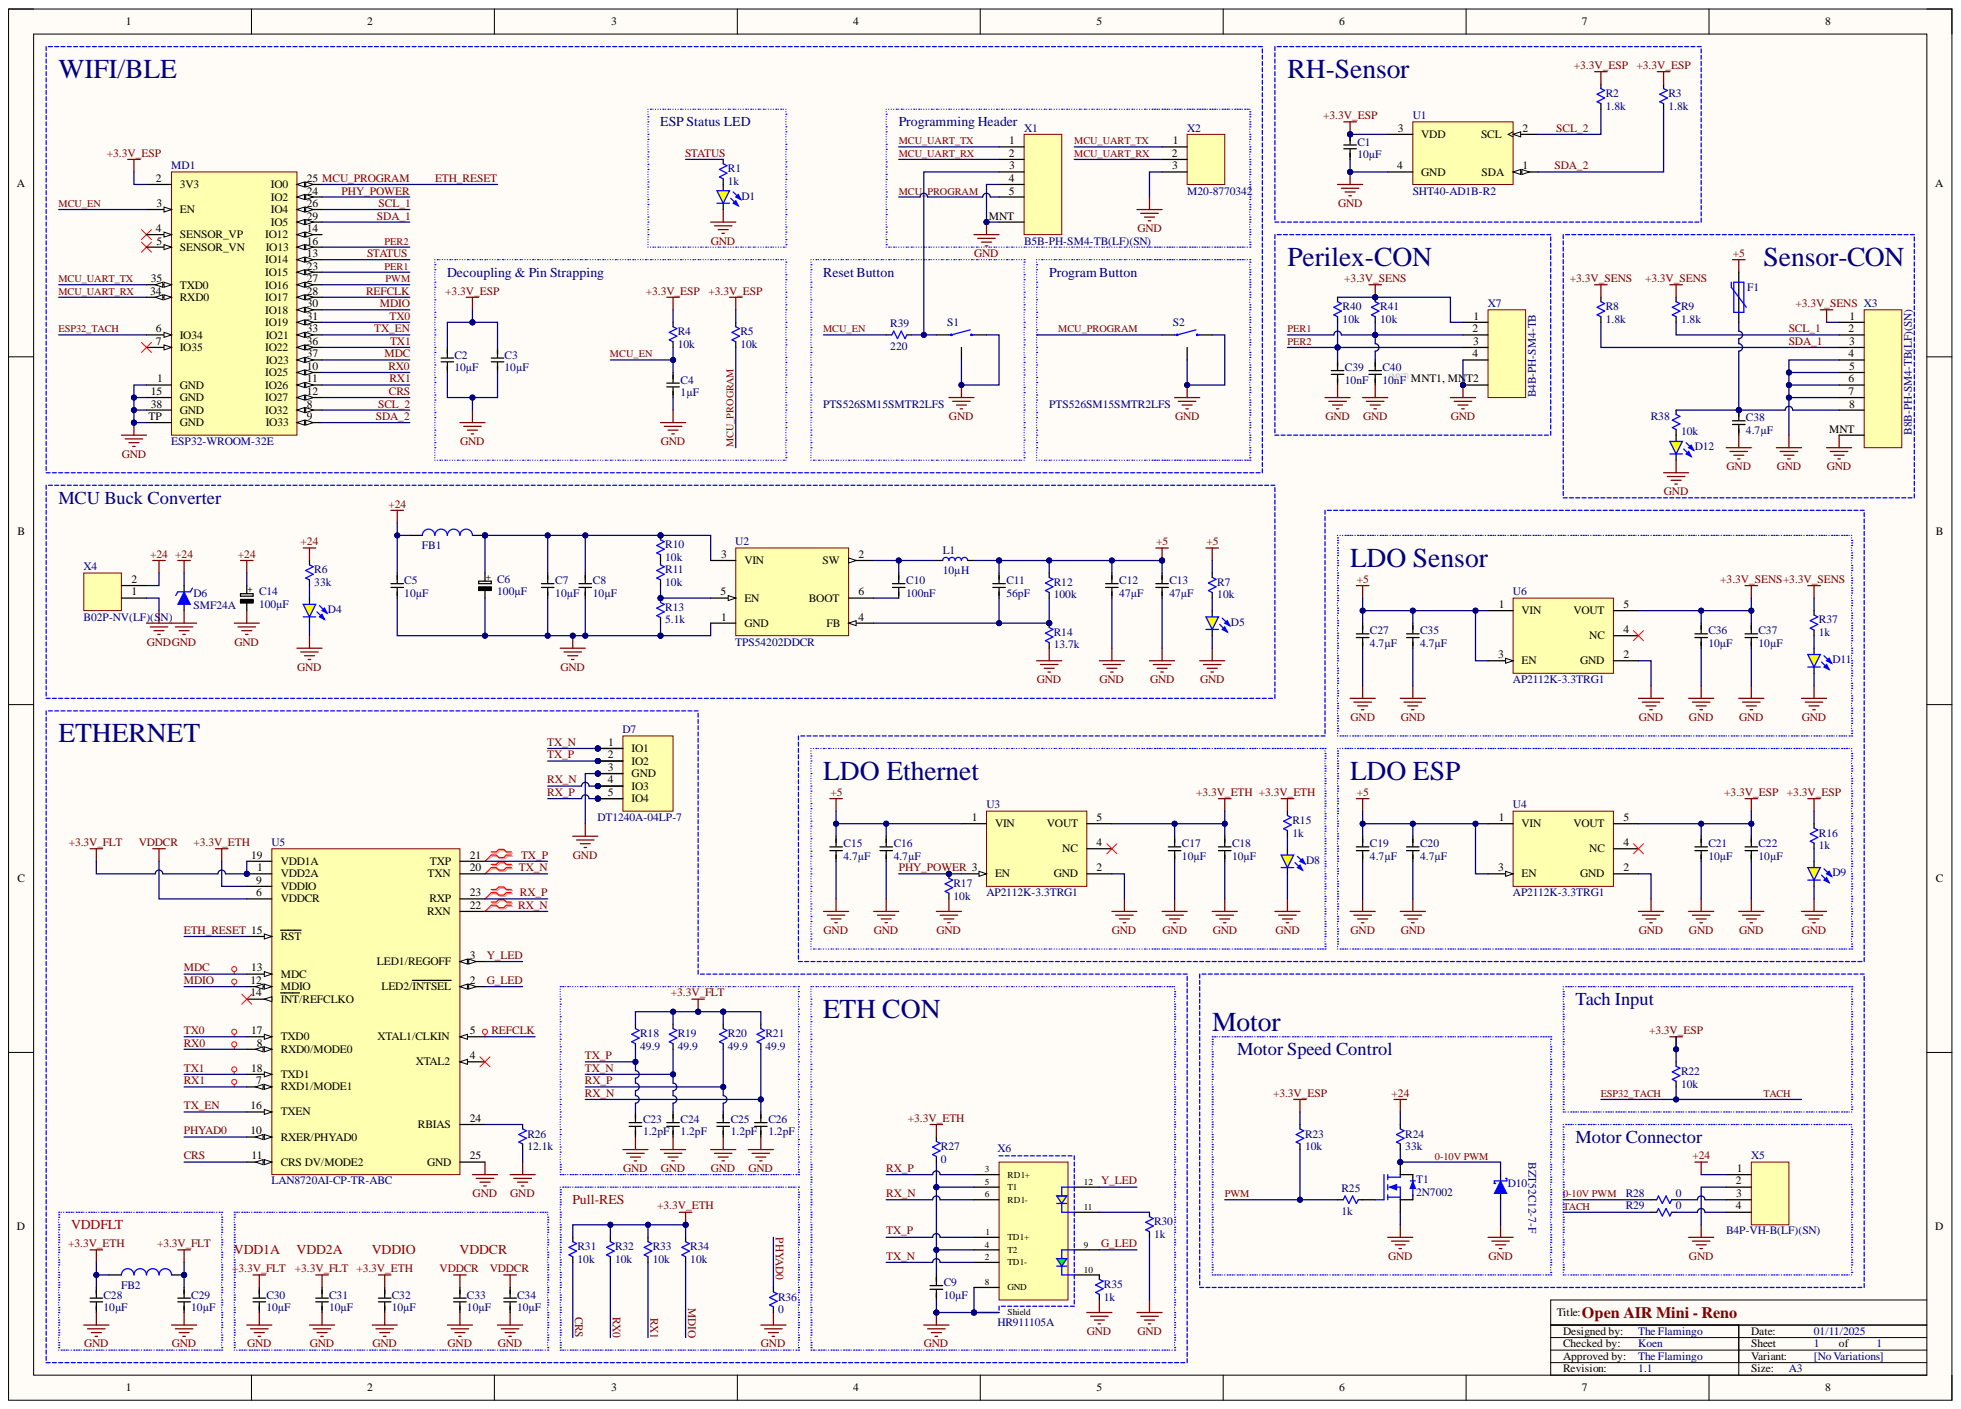
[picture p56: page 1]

Open AIR Mini - Reno
Title:
Approved by: The Flamingo
Revision:

Line# | Name | Description | Designator | Quantity | Fitted | LCSCPart Number | LCSCJellyBean Part Number | Revision Status | Revision State | JLCPCBBasicPart
| 74437336100 | General PurposeInductor, 10uH,20%,1 Element,Powdered Iron-Core,SMD,2220 | L1 | 1 | | C2045810 | C177248 | | Unknown server
| BZT52C12-7-F | Zener Diode,12VV(Z),5.39%,0.37W,Silicon,Unidirectional | D10 | 1 | | C124196 | - | | Unknown server
| DT1240A-04LP-7 | TransVoltageSuppressor Diode,52W,3.3VV(RWM),Unidirectional,1 Element,Silicon | D7 | 1 | | C5248968 | C22363670 | | Unknown server
| ERJ-2RKF1372X | RES,SMT,13.7kΩ,1%,100mW,100ppm/°C 0402 | R14 | 1 | | C2076881 | C25854 | | Unknown server
| ERJ-2RKF1801X | RES,SMT,1.8kΩ,1%,100mW,100ppm/°C 0402 | R2,R3,R8,R9 | 4 | | C400611 | C163481 | | Unknown server
| GRM32EC81C476KE15K | CAPMLCC1210 47uF10%16VX7R | C12,C13 | 2 | | C3831429 | C5440143 | | Unknown server
| SMF24A | TransVoltageSuppressor Diode,200W,24VV(RWM),Unidirectional,1 Element,Silicon | D6 | 1 | | C315999 | C19077514 | | Unknown server
| TPS54202DDCR | Switching Regulator, Current-mode,2A,500kHzSwitching Freq-Max, PDSO6 | U2 | 1 | | C191884 | - | | Unknown server
| 1206L050/24WR | PTCResettableFuse,SurfaceMount | F1 | 1 | | C2154056 | C369160 | | Unknown server
| 865230557006 | WCAP-AS5H Aluminum Electrolytic Capacitors | C6,C14 | 2 | | - | C3148158 | | Unknown server
| AP2112K-3.3TRG1 | Fixed PositiveLDORegulator, 3.3V,0.4VDropout,CMOS,PDSO5 | U3,U4,U6 | 3 | | C51118 | - | | Unknown server
| B02P-NV(LF)(SN) | NVSeries2 Position 5 mm Pitch Through HoleLocking Header | X4 | 1 | | C160287 | C5441119 | | Unknown server
| B5B-PH-SM4-TB(LF)(SN) | B5B-PH-SM4-TB(LF)(SN) | X1 | 1 | | C265085 | C7433666 | | Unknown server
| B8B-PH-SM4-TB(LF)(SN) | Connector Header,PH Series,8 Position,2.00mm,100V,Surface Mount,Solder, Natural. | X3 | 1 | | C265441 | C2845457 | | Unknown server
| ESP32-WROOM-32E | WiFi-Modul 802.11/BT2,4-2,5GHz150Mb/s | MD1 | 1 | | C701341 | - | | Unknown server
| HR911105A | 100mbit connector with integrated magnetics | X6 | 1 | | C12074 | - | | Unknown server
| LAN8720AI-CP-TR-ABC | Ethernet Transceiver | U5 | 1 | | C510876 | - | | Unknown server
| SHT40-AD1B-R2 | Senserion Moisture and TemperatureSensor | U1 | 1 | | C2909890 | - | | Unknown server
| B4B-PH-SM4-TB | 2.0mm pitch/DisconnectableInsulation displacement and Crimp style connectors | X7 | 1 | | C160354 | C2763704 | | Unknown server | No
| B4P-VH-B(LF)(SN) | Locking Header, Top EntryTypeof PBT,4 Circuit,3.96mmPitch | X5 | 1 | | C493148 | C8884 | | Unknown server | No
| ERJ-2RKF49R9X | RES,SMT,49.9Ω,1%,100mW,100ppm/°C 0402 | R18,R19,R20,R21 | 4 | | C441726 | C25120 | | Unknown server | No
| ERJ-2RKF1212X | RES,SMT,12.1kΩ,1%,100mW,100ppm/°C 0402 | R26 | 1 | | C416469 | C25852 | | Unknown server | No
| GRM1555C1H560JA01J | CAPMLCC0402 56pF5%50VC0G0402 | C11 | 1 | | C6204182 | C1572 | | Unknown server | No
| M20-8770342 | Header SMTMALE3 Pin 1 Row 2.54mm Pitch Vertical Gold Plated | X2 | 1 | | C5757760 | C2883760 | | Unknown server | No
| 2N7002 | Small Signal Field-Effect Transistor, 0.115AI(D),60V,1-Element,N-Channel,Silicon,Metal-oxideSemiconductor FET | T1 | 1 | | - | C8545 | | Unknown server | Yes
| 0402WGF2200TCE | RES,SMT,220Ω,1%,63.5mW,100ppm/°C 0402 | R39 | 1 | | C25091 | - | | Unknown server | Yes
| 150060WS75000 | SMDMono-color Chip LEDs | D1,D4,D5,D8,D9,D11,D12 | 7 | | | C2290 | | Unknown server | Yes
| 74279204 | FerriteBead,1 Function(s),0.5A,2 Pin(s) | FB1,FB2 | 2 | | - | C1017 | | Unknown server | Yes
| CGA2B3X7R1H104K050B B | CAPMLCC0402 100nF10%50VX7R0402 | C10 | 1 | | C2167391 | C307331 | | Unknown server | Yes
| CL05A106MQ5NUNC | CAPMLCC0402 10uF20%6.3VX5R0402 | C1,C2,C3,C9,C17,C18,C21, C22,C28,C29,C30,C31,C32, C33,C34,C36,C37 | 17 | | C15525 | - | | Unknown server | Yes
| CL05A475MP5NRNC | CAPMLCC0402 4.7uF20%10vVX5R0402 | C15,C16,C19,C20,C27,C35, C38 | 7 | | C23733 | - | | Unknown server | Yes
| CL31A106KBHNNNE | CAPMLCC1206 10uF10%50VX5R | C5,C7,C8 | 3 | | C13585 | - | | Unknown server | Yes
| ERJ-2RKF1001X | RES,SMT,1kΩ,1%,100mW,100ppm/°C 0402 | R1,R15,R16,R25,R30,R35, R37 | 7 | | C242161 | C11702 | | Unknown server | Yes
| ERJ-2RKF1002X | RES,SMT,10kΩ,1%,100mW,100ppm/°C 0402 | R4,R5,R7,R10,R11,R17, R22,R23,R31,R32,R33,R34, R38,R40,R41 | 15 | | C191123 | C25744 | | Unknown server | Yes
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

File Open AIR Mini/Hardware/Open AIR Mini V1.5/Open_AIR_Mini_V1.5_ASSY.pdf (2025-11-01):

## Fabrication Specifications

# Fabrication Information

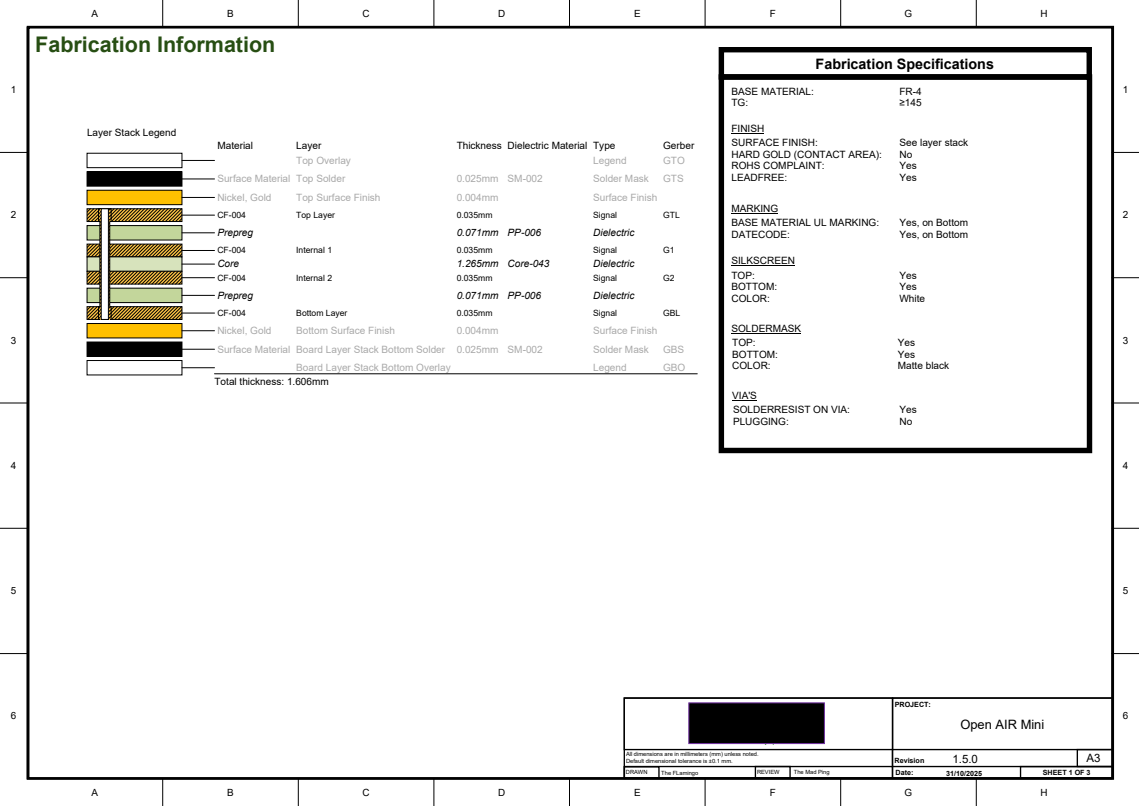
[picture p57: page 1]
Material; Layer; Thickness Dielectric Material Type; Gerber; Top Overlay; Legend; GTO; Surface Material Top Solder; Solder Mask; GTS; Nickel, Gold; Top Surface Finish; Surface Finish; Top Layer; Signal; GTL; Prepreg; Dielectric; Internal 1; Core; 1.265mm Core-043; Internal 2; Bottom Layer; GBL; Bottom Surface Finish; Surface Material Board Layer Stack Bottom Solder 0.025mm SM-002; GBS; Board Layer Stack Bottom Overlay; GBO; Total thickness: 1.606mm; Yes No; Yes Yes Matte black; Yes Yes White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

FINISH
SURFACE FINISH:
HARD GOLD (CONTACT AREA):
ROHS COMPLAINT:
LEADFREE:

Layer Stack Legend

See layer stack
Yes

MARKING
BASE MATERIAL UL MARKING:
DATECODE:

Yes, on Bottom

VIA'S
SOLDERRESIST ON VIA:
PLUGGING:

Open AIR Mini

All dimensions are in millimeters (mm) unless noted.
Default dimensional tolerance is ±0.1 mm.
DRAWN

# Component Placement - Top & Bottom

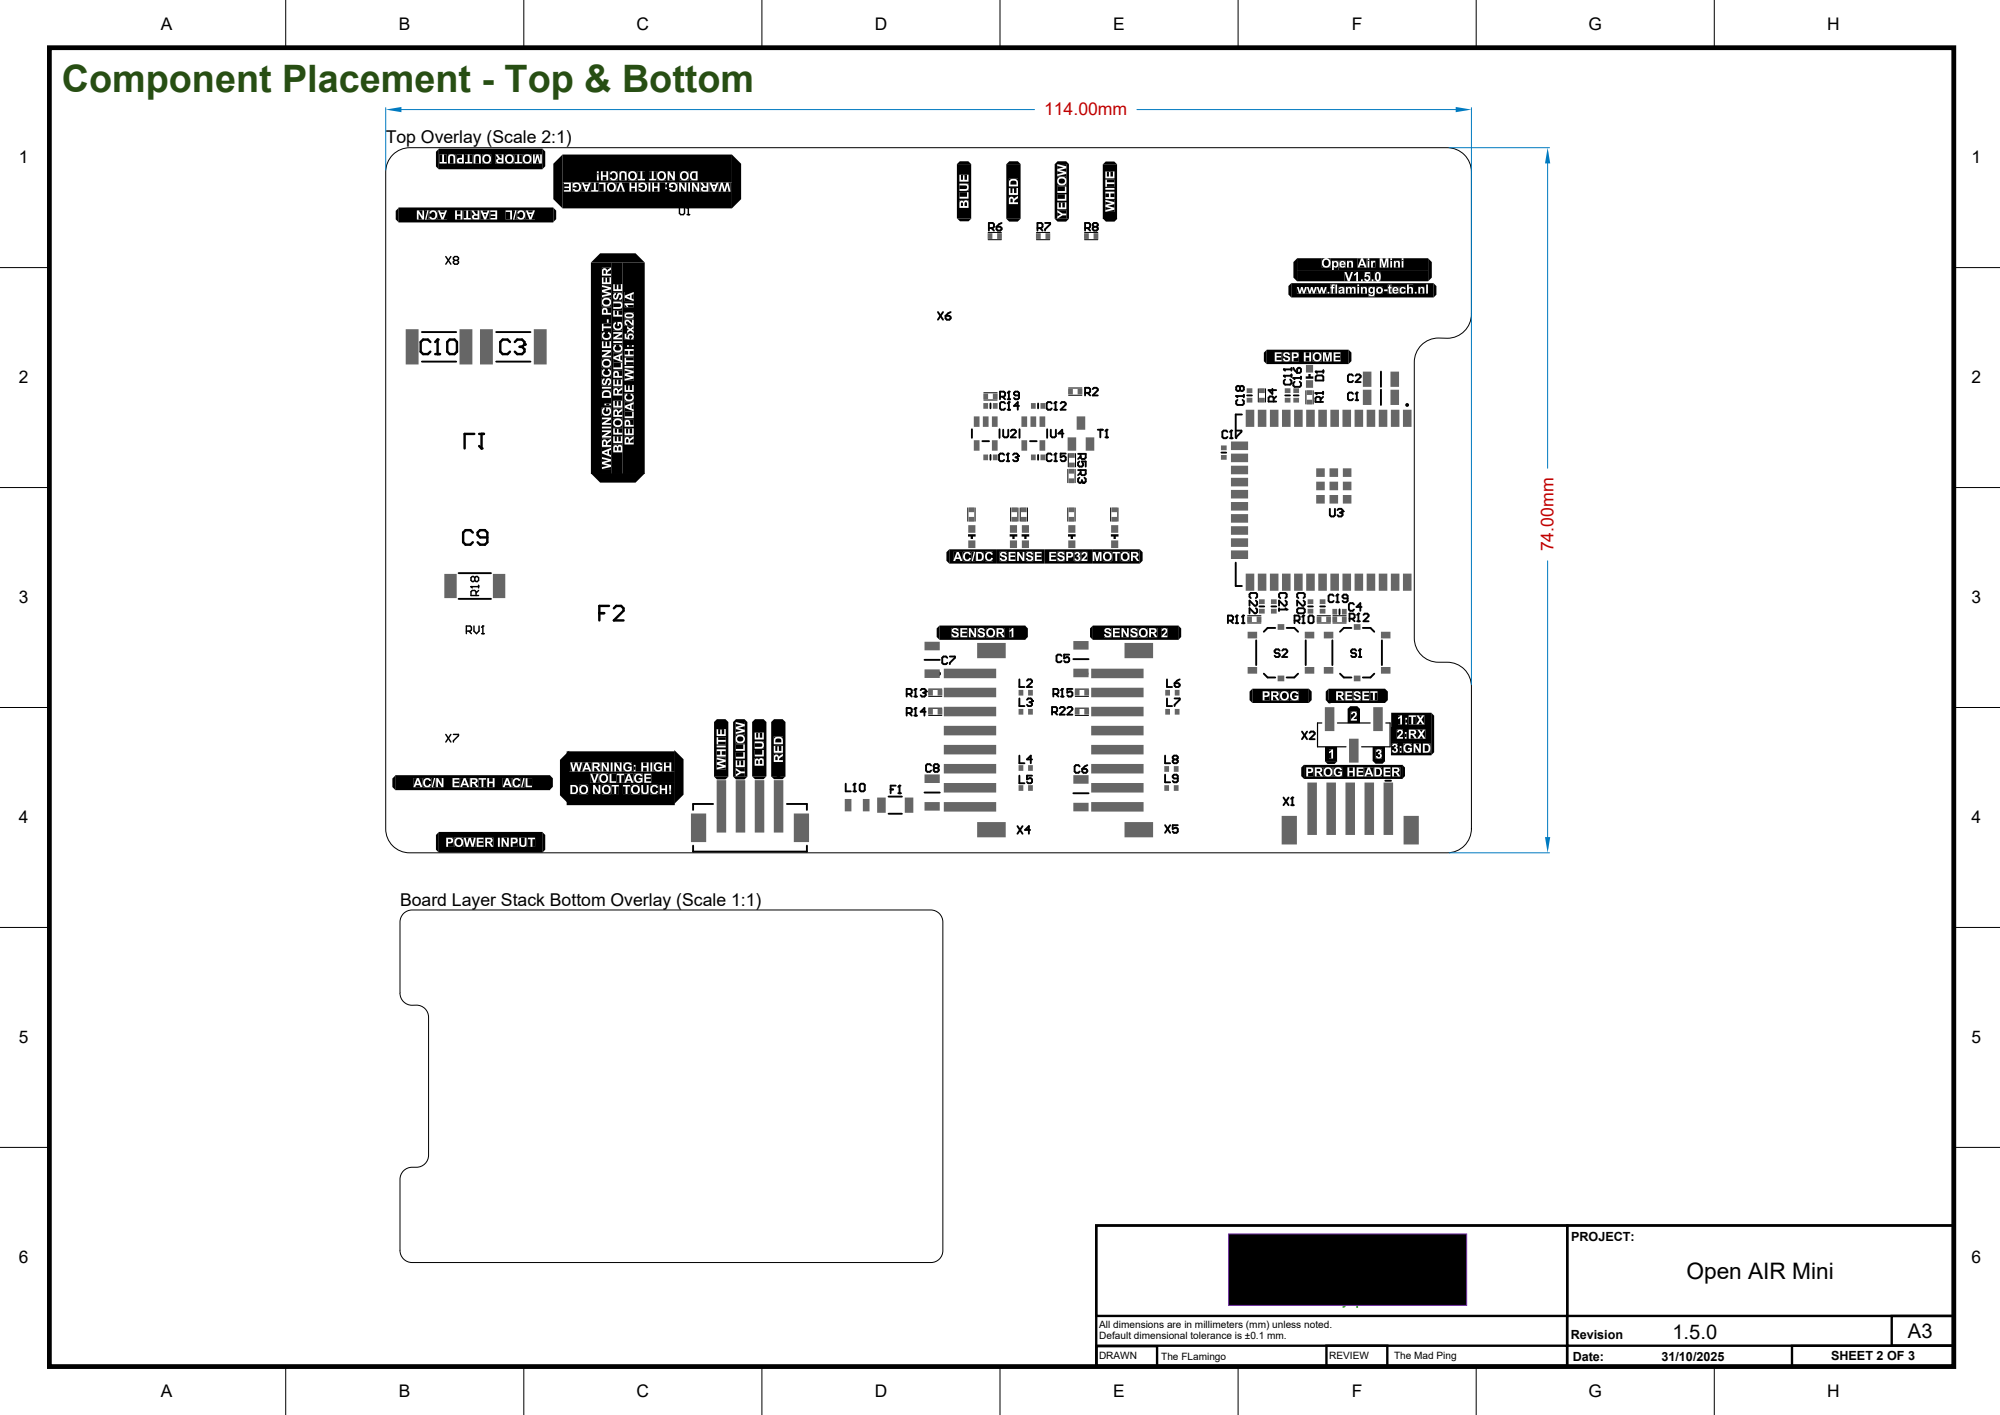
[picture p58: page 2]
PROJECT:

Top Overlay (Scale 2:1)

Board Layer Stack Bottom Overlay (Scale 1:1)

Open AIR Mini

# Realistic view - TOP & BOT

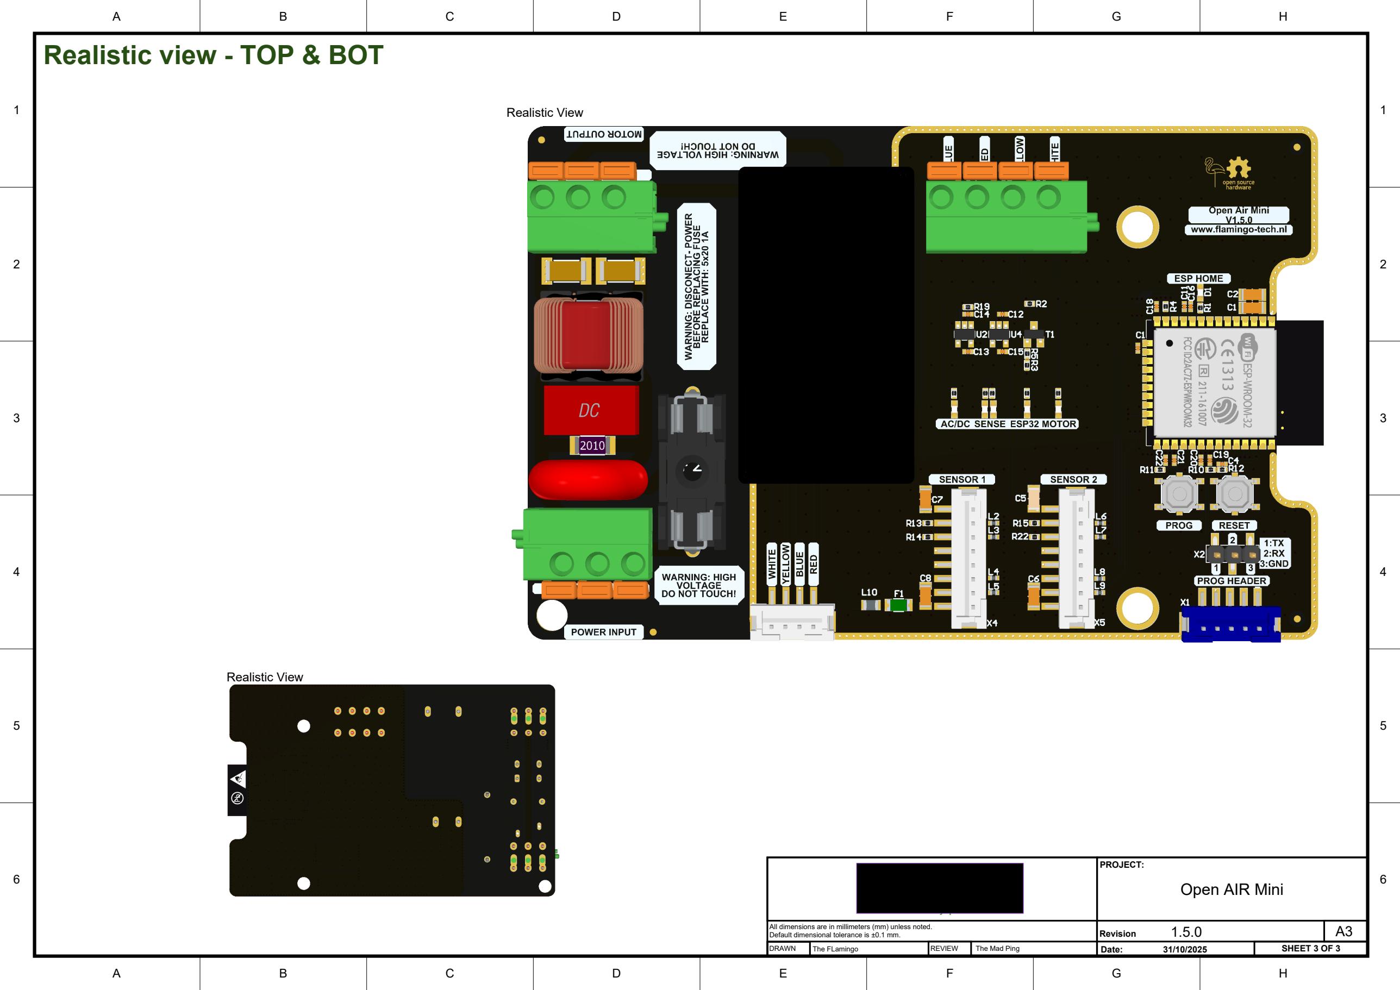
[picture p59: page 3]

1 | 1
2 | 2
3 | 3
4 | 4
5 | 5
6 | 6

Realistic View

PROJECT:

## Open AIR Mini

Realistic View

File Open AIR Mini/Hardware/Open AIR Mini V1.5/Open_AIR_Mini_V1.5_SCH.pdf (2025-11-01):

# WIFI/BLE

## ESP32


AC/DC Status LED

ESP LDO Status LED

Sens LDO Status LED

Title:
Approved by: The Mad Ping

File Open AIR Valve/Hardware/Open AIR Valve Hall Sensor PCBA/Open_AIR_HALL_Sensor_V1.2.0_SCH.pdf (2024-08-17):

# Open AIR

# Valve Hall Sensor


B3B-XH-A(LF)(SN) GND

Open AIR
Title:
Approved by: The Flamingo
Revision:

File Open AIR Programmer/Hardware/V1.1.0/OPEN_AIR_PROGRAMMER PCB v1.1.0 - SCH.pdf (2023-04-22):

# USB-> UART Converter

# USB Connector


Title:
Approved by: The Mad Ping

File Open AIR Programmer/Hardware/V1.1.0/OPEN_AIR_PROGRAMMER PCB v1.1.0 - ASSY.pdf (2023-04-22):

## Fabrication Specifications

# Fabrication information

Material; Layer; Thickness Dielectric Material Type; Gerber; Top Overlay; Legend; GTO; Surface Material Top Solder; Solder Mask; GTS; Nickel, Gold; Top Surface Finish; Surface Finish; Top Layer; Signal; GTL; Prepreg; Dielectric; Layer 1; Core; 1.065mm Core-043; Layer 2; Bottom Layer; GBL; Bottom Surface Finish 0.017mm; Surface Material Bottom Solder; GBS; Bottom Overlay; GBO; Total thickness: 1.635mm; Yes No; Yes Yes Matte black; Yes Yes White; TOP: BOTTOM: COLOR:; SOLDERMASK; SILKSCREEN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

Layer Stack Legend

FINISH
SURFACE FINISH:
HARD GOLD (CONTACT AREA):
ROHS COMPLAINT:
LEADFREE:

See layer stack
Yes

MARKING
BASE MATERIAL UL MARKING:
DATECODE:

Yes, on Bottom

VIA'S
SOLDERRESIST ON VIA:
PLUGGING:

Reference layers
Layer 1
Top Layer,Layer 2
Layer 1,Bottom Layer
Layer 2

Substack
Board Layer Stack

# Component placement - TOP & BOT

Top Overlay (Scale 5:1); Bottom Overlay (Scale 5:1)

1 | 1
2 | 2
3 | 3
4 | 4
5 | 5
6 | 6


Realistic View

# Realistic view - TOP & BOT


Realistic View

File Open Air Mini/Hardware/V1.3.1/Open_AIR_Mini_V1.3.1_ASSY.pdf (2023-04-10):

## Fabrication Specifications

# Fabrication information

Material; Layer; Thickness Dielectric Material Type; Gerber; Top Overlay; Legend; GTO; Surface Material Top Solder; Solder Mask; GTS; Nickel, Gold; Top Surface Finish; Surface Finish; Top Layer; Signal; GTL; Prepreg; Dielectric; Internal 1; Core; 1.265mm Core-043; Internal 2; Bottom Layer; GBL; Bottom Surface Finish; Surface Material Board Layer Stack Bottom Solder 0.025mm SM-002; GBS; Board Layer Stack Bottom Overlay; GBO; Total thickness: 1.606mm; Yes No; Yes Yes Matte black; Yes Yes White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

Layer Stack Legend

FINISH
SURFACE FINISH:
HARD GOLD (CONTACT AREA):
ROHS COMPLAINT:
LEADFREE:

See layer stack
Yes

MARKING
BASE MATERIAL UL MARKING:
DATECODE:

Yes, on Bottom

VIA'S
SOLDERRESIST ON VIA:
PLUGGING:

# Component placement - TOP & BOT

Top Overlay (Scale 2:1); Board Layer Stack Bottom Overlay (Scale 2:1)

# Realistic view - TOP & BOT


1 | 1
2 | 2
3 | 3
4 | 4
5 | 5
6 | 6

Realistic View
Realistic View

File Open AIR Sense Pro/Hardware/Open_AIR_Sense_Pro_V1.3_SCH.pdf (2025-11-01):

WIFI/BLE | FID1

# QWIIC


SM04B-SRSS-TB(LF)(SN)

Open AIR Sense Pro
Title:
Approved by: The Flamingo
Revision:

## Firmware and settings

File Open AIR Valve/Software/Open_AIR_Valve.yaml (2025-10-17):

## Written for Esphome version: 2025.9.1 
substitutions:
  # --- per-device names ---
  devicename: open-air-valve-1          # Lowercase, no spaces
  upper_devicename: Open AIR Valve 1    # UI Name

esphome:
  name: ${devicename}
  name_add_mac_suffix: true
  on_boot:
    - priority: 700
      then:
        # Instant accel/decel as before
        - stepper.set_acceleration:
            id: my_stepper
            acceleration: inf
        - stepper.set_deceleration:
            id: my_stepper
            deceleration: inf

        # Start from known 0 and move to 10% (index 10 in LUT)
        - stepper.report_position:
            id: my_stepper
            position: 0
        - stepper.set_target:
            id: my_stepper
            target: !lambda 'return id(valve_capacity_lookup_table)[10];'
        - wait_until:
            condition:
              lambda: |-
                return id(my_stepper).current_position == id(my_stepper).target_position;

        - stepper.set_speed:
            id: my_stepper
            speed: 250 steps/s

        # Home if needed (original sequence preserved)
        - if:
            condition:
              binary_sensor.is_off: valve_homing_switch
            then:
              - while:
                  condition:
                    binary_sensor.is_off: valve_homing_switch
                  then:
                    - stepper.report_position:
                        id: my_stepper
                        position: 0
                    - stepper.set_target:
                        id: my_stepper
                        target: -1
                    - wait_until:
                        condition:
                          lambda: |-
                            return id(my_stepper).current_position <= id(my_stepper).target_position;

        # Re-zero after homing; stop at 0
        - stepper.report_position:
            id: my_stepper
            position: 0
        - stepper.set_target:
            id: my_stepper
            target: 0
        - stepper.set_speed:
            id: my_stepper
            speed: 250 steps/s

        # Publish a coherent starting state (optimistic)
        - lambda: |-
            id(last_cmd_pos) = 0.0f;
            id(air_valve).position = id(last_cmd_pos);
            id(air_valve).current_operation = VALVE_OPERATION_IDLE;
            id(air_valve).publish_state();

esp32:
  board: esp32dev
  framework:
    type: esp-idf

logger:
  level: DEBUG

web_server:
  port: 80

script: !include disconnected-mode.yaml

api:
  encryption:
    key: !secret api_encryption_key
  on_client_disconnected:
    - script.execute: disconnected_mode
  services:
    - service: control_stepper
      variables:
        target: int
      then:
        - lambda: |-
            int s = target;
            if (s < 0) s = 0;
            if (s > 525) s = 525;
            id(my_stepper).set_target(s);

ota:
  - platform: esphome
    password: !secret ota_password

wifi:
  ssid: !secret wifi_ssid
  password: !secret wifi_password
  ap:
    ssid: "${upper_devicename} Config AP"
    password: !secret wifi_ap_password

captive_portal:

# ---------- GLOBALS ----------
globals:
  - id: valve_capacity_lookup_table
    type: std::vector<int>
    restore_value: no
    initial_value: '{0,47,66,82,94,106,116,125,134,142,150,158,165,172,178,185,191,197,203,209,215,220,225,231,236,241,246,251,256,261,265,270,275,279,284,288,292,297,301,305,309,314,318,322,326,330,334,338,342,346,350,353,357,361,365,368,372,376,380,383,387,391,394,398,401,405,409,412,416,419,423,426,430,433,437,440,443,447,450,454,457,461,464,467,471,474,478,481,484,488,491,494,498,501,504,508,511,514,518,521,525}'
  # Remember last commanded valve position (0.0..1.0), restored on boot
  - id: last_cmd_pos
    type: float
    restore_value: yes
    initial_value: '0.0'
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

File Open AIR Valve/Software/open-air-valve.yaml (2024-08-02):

esphome:
  name: "open-air-valve-x"
  name_add_mac_suffix: true
  platform: ESP32
  board: esp32dev

  on_boot:
    - priority: 700
      then:
      - stepper.set_acceleration:
          id: my_stepper
          acceleration: inf
      - stepper.set_deceleration:
          id: my_stepper
          deceleration: inf
      - stepper.report_position:
          id: my_stepper
          position: 0
      - stepper.set_target:
          id: my_stepper
          target: !lambda 'return id(valve_capacity_lookup_table)[10];'
      - wait_until:
          condition:
            lambda:
              return id(my_stepper).current_position == id(my_stepper).target_position;
      - stepper.set_speed:
          id: my_stepper
          speed: 150 steps/s
      - if:
          condition:
            binary_sensor.is_off: valve_homing_switch
          then:
          - while:
              condition:
                binary_sensor.is_off: valve_homing_switch
              then:
                - stepper.report_position:
                    id: my_stepper
                    position: 0
                - stepper.set_target:
                    id: my_stepper
                    target: -1
                - wait_until:
                    condition:
                      lambda:
                        return id(my_stepper).current_position <= id(my_stepper).target_position;
      - stepper.report_position:
          id: my_stepper
          position: 0
      - stepper.set_target:
          id: my_stepper
          target: 0
      - stepper.set_speed:
          id: my_stepper
          speed: 350 steps/s

# Enable logging
logger:
  level: DEBUG

# This is optional and can be commented out to disable the Web Server
web_server:
  port: 80

# Enable Home Assistant API
api:
  services:
  - service: control_stepper
    variables:
      target: int
    then:
      - stepper.set_target:
          id: my_stepper
          target: !lambda 'return target;'

ota:
  password: "9f2ab9aa715f573e2476e75a5ec7f4e7"

wifi:
  ssid: !secret wifi_ssid
  password: !secret wifi_password

  # Enable fallback hotspot (captive portal) in case wifi connection fails
  ap:
    ssid: "Open AIR Valve Config AP"
    password: "ChangeMe@123!"
    
captive_portal:

globals:
  - id: valve_capacity_lookup_table
    type: std::vector<int>
    restore_value: no
    initial_value: '{0,47,66,82,94,106,116,125,134,142,150,158,165,172,178,185,191,197,203,209,215,220,225,231,236,241,246,251,256,261,265,270,275,279,284,288,292,297,301,305,309,314,318,322,326,330,334,338,342,346,350,353,357,361,365,368,372,376,380,383,387,391,394,398,401,405,409,412,416,419,423,426,430,433,437,440,443,447,450,454,457,461,464,467,471,474,478,481,484,488,491,494,498,501,504,508,511,514,518,521,525}'

number:
  - platform: template
    name: "Valve Capacity %"
    id: valve_capacity
    optimistic: true
    restore_value: no
    initial_value: 0
    min_value: 0
    max_value: 100
    step: 10
    mode: slider
    on_value:
      then:
        - stepper.set_target:
            id: my_stepper
            target: !lambda |-
              if (x <= 0) { 
                return 0; 
              } else if(x >= 100) {
                return 525;
              } else if (x > 0 && x < 100) {
                int steps = id(valve_capacity_lookup_table)[x];
                return steps;
              } else {
                return 0;
              }

status_led:
  pin:
    number: GPIO33

uart:
#UART For Sensor 1
-  id: uart_sensor_1
   rx_pin: GPIO25
   tx_pin: GPIO26
   baud_rate: 9600


i2c:
#I2C For Sensor 1
- id: i2c_sensor_1
  sda: GPIO16
  scl: GPIO4
  scan: false
  frequency: 400kHz
  
cover:
  - platform: template
    name: "Valve"
    id: valve
    lambda: |-
      if (id(my_stepper).current_position <= 0) {
        return COVER_CLOSED;
      } else if (id(my_stepper).current_position > 0 && id(my_stepper).current_position <= 100) {
        return COVER_OPEN;
      } else {
        return {};
      }
    open_action:
      - number.set:
          id: valve_capacity
          value: 100
      - stepper.set_target:
          id: my_stepper
          target: 525
    close_action:
      - number.set:
          id: valve_capacity
          value: 0
      - stepper.set_target:
          id: my_stepper
          target: 0

stepper:
  - platform: uln2003
    id: my_stepper
    pin_a: GPIO15
    pin_b: GPIO14
    pin_c: GPIO13
    pin_d: GPIO12
    max_speed: 350 steps/s
    acceleration: inf
    deceleration: inf
    sleep_when_done: true
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

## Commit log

2022-11-05 Added Open Air Valve.PDF
    More information about connector use/Mating parts
2022-11-13 Removed Files
    [Open AIR Valve Bottom PETG_0.4n_A.3mf, Open AIR Valve Bottom PETG_0.6n_A.3mf, Open AIR Valve Bottom_A.step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]
2022-11-27 Update README.md
    removed valve added mini options
2022-11-27 Create SHT20.H
    added SHT20.h sensor
2022-12-10 added image to landing readme
2022-12-10 added valve image
2022-12-10 added valve example image
2022-12-18 Added Gerber & Schematic
    Added Gerber & Schematic
2023-01-06 Update README.md
    added explanation about sensor1/2
2023-01-06 Update README.md
    Corrected sensor mistake
2023-01-06 Update README.md
    clarify sensor use
2023-04-10 Added Valve Gerbers & Mini Gerbers
    Added Valve Gerbers & Mini Gerbers
    [Open_AIR_Mini_V1.3.1_B.O.M.xlsx, Open_AIR_Valve_V1.3.0_B.O.M.xlsx]
2023-04-22 added multi sensor
    added multi sensor
2023-04-22 Added more info
    Added programmer info + changed pictures
    [OPEN_AIR_PROGRAMMER PCB v1.1.0 - BOM.xlsx]
2023-04-22 Added version numbers to MD file
    [Open_AIR_Mini_V1.3.1_B.O.M.xlsx]
2023-04-23 Moved & Changed AIR Valve Pictures
2023-04-23 Added more info on the Open AIR Valve
2023-10-14 Update README.md
    Updated Sensor table :)
2024-01-12 added programming guide
    [Open_AIR_Mini_V1.3.1_B.O.M.xlsx]
2024-03-02 changed to V1.4.1 AIR MINI
    [Open_AIR_Mini_V1.3.1_B.O.M.xlsx]
2024-03-24 Update open-air-mini.yaml
    Fix for Sensor label swap
    [open-air-mini.yaml]
2024-04-05 merged both Open AIR Valve Repo's
    Love you Thomasvnl <3
2024-04-06 Changed Valve Sensor Support
    Added new sensors and changed support for Hall sensor homing.
2024-04-15 Changed Sensor support
2024-04-22 sensor: fix scd4x config
2024-04-27 Added Step files :) + minor changes
    [Open_AIR_Mini_V1.3.1_B.O.M.xlsx, Open_AIR_Sensor_Housing_Duco_Bottom_B.step, Open_AIR_Sensor_Housing_Duco_Top_B.step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]
2024-05-22 reverse valve opening direction
    [open-air-valve.yaml]
2024-06-07 Add files via upload
    Fixed issue with housing step file
    [Open_AIR_Valve_Bottom_A.step]
2024-06-16 Wifi signal strenght sensor added
2024-06-16 added Stickers
    [ESW-0ZAA-EU-Sticker Align Jig.obj]
2024-08-17 Added Open AIR Valve Hall Sensor Info
    [Open_AIR_HALL_Sensor_V1.2.0_BOM.xlsx]
2024-08-17 added small Read me for HALL sensor SCH
2024-08-17 Fixed issue with BOM
    [Open_AIR_HALL_Sensor_V1.2.0_BOM.xlsx]
2025-02-21 Delete Open AIR Mini/Software/SHT20.H
    Not needed anymore after fix by Donny Maasland : https://github.com/Flamingo-tech/Open-AIR/tree/main/Open%20AIR%20Mini/Software#sensor-support-SHT-20
2025-03-21 Added Insert-less 3D prints for the Valves
    Added Insert-less 3D prints for the Valves
    [Open_AIR_Valve_Bottom_A.step, Open_AIR_Valve_Bottom_C.step, Open_AIR_Valve_Disc_B.step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]
2025-03-22 Added New Valve DIY BOM
2025-09-28 Updated Valve Yaml to V1.1.0
    See change log for all changes
2025-09-28 Updated Readme.YAML
    added support for ${upper_devicename} in sensor names
2025-11-01 Added Source files for, Open AIR Mini, Reno , Valve , Sense Pro
    [Open_AIR_Mini_Reno_V1.1_BOM.xlsx, Open_AIR_Mini_Reno_V1.1_PNP.csv, Open_AIR_Mini_V1.5_BOM.xlsx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]
